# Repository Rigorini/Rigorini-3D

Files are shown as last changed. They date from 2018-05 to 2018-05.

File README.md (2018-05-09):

# Rigorini 3D
A big, cheap and accurate dual extruder FDM 3D Printer.

You can build it under 400,00 €!!

***

[Check the WIKI to understand the key features!](https://github.com/Rigorini/Rigorini-3D/wiki)

***

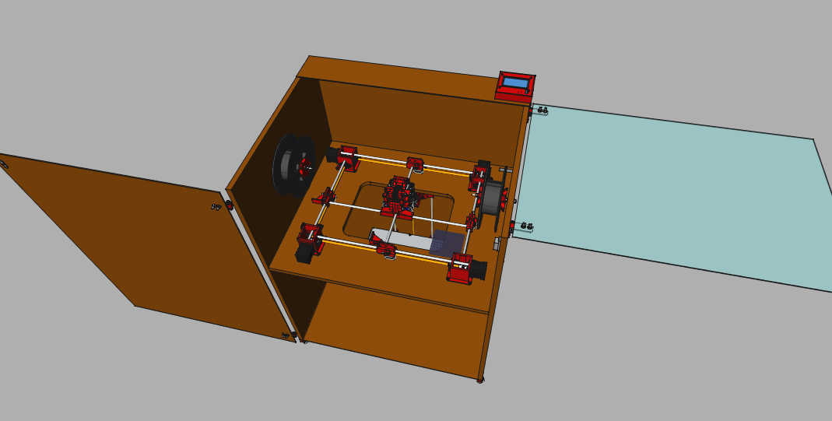
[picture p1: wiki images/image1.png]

Opened view

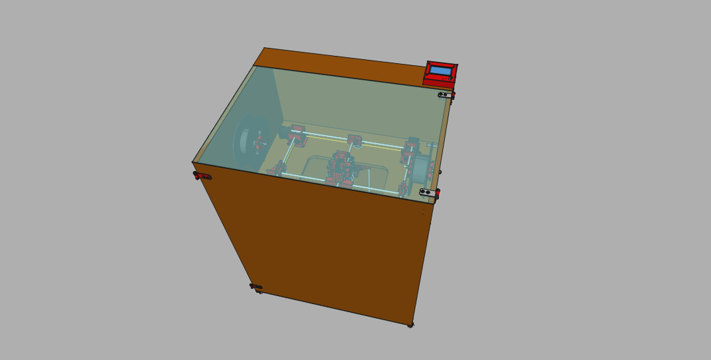
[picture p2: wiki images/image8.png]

Closed view

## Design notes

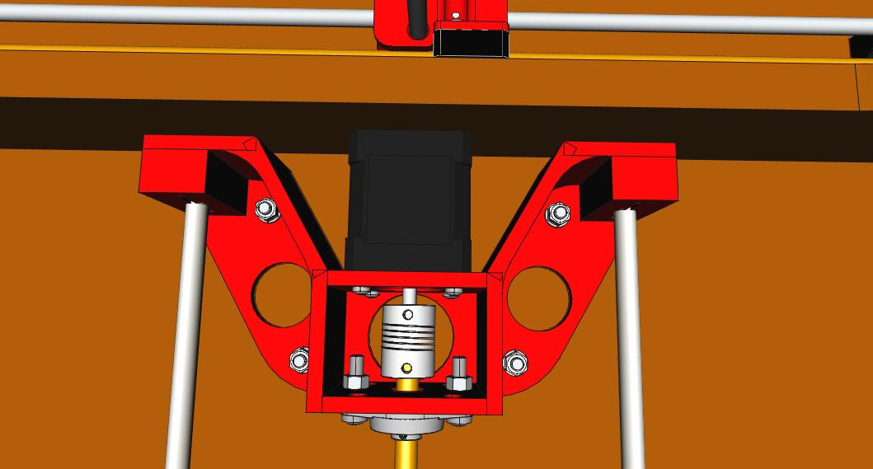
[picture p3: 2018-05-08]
wiki images/images12.png

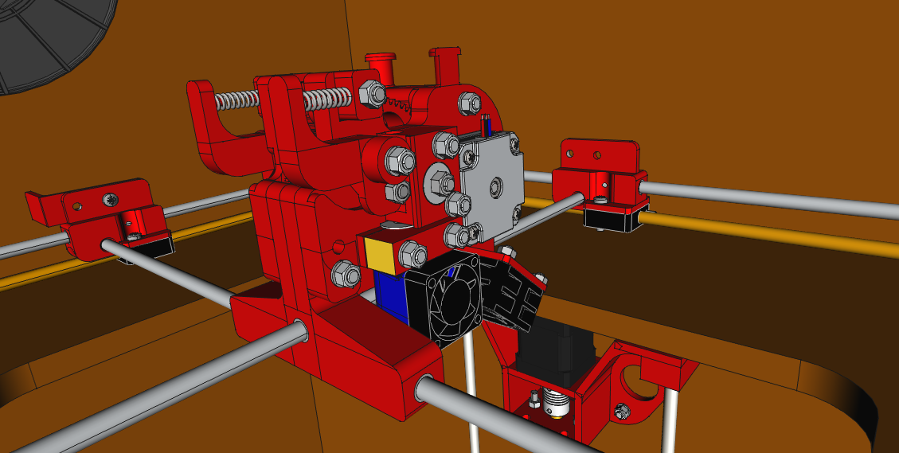
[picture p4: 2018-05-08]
wiki images/images9.png

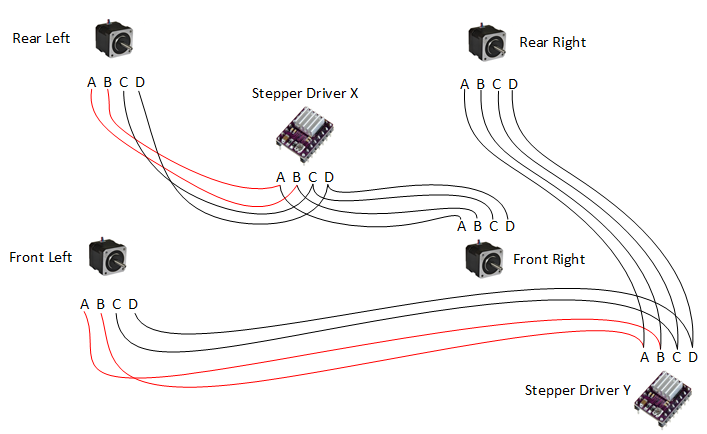
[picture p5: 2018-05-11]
wiki images/Steppers Schema.png

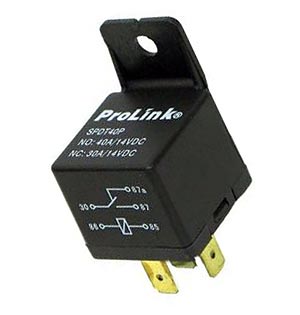
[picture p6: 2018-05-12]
wiki images/Relay.jpg

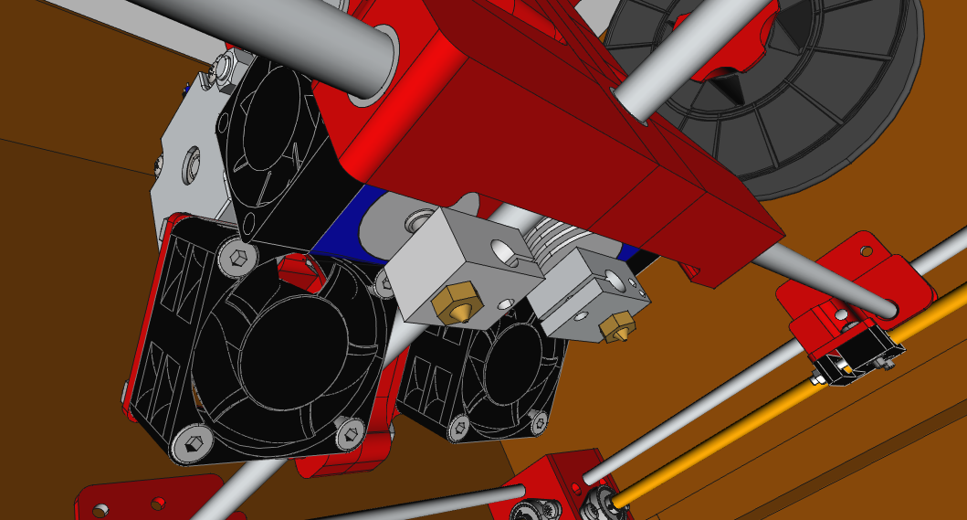
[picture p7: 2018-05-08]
wiki images/images11.png

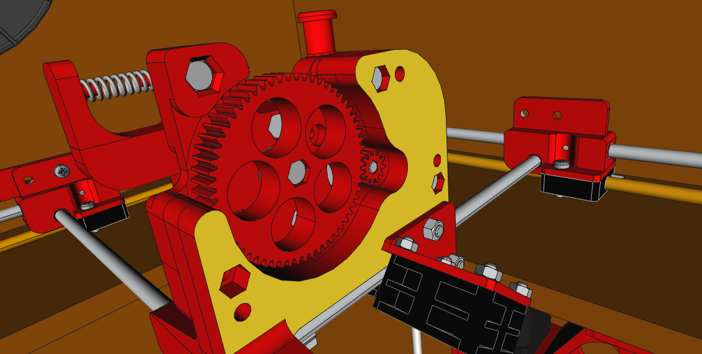
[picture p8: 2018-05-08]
wiki images/images10.png

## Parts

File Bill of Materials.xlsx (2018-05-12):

Description | Quantity | Where to buy | Estimate unit price | Total price
Alluminium sheet 215x315x2 | 1 | Local store | 3.00 € | 3.00 €
Arduino Mega 2560 | 1 | Aliexpress | 10.00 € | 10.00 €
Bearings 625zz | 10 | Aliexpress | 0.15 € | 1.50 €
Bearings KFL08 | 10 | Aliexpress | 1.50 € | 15.00 €
Bed level Spring | 3 | Aliexpress | 0.50 € | 1.50 €
Bolts 5x20 | 6 | Local store
Bolts 5x30 | 33 | Local store
Bolts 5x40 | 2 | Local store
Bushing Sleeve SF-1 0810 | 16 | Aliexpress | 0.28 € | 4.40 €
DRV8825 Stepper Driver | 5 | Aliexpress | 1.00 € | 5.00 €
Endstop Mechanical Switches | 3 | Aliexpress | 1.50 € | 4.50 €
Extruder E3D V6 with Fan (Direct) | 2 | Aliexpress | 6.00 € | 12.00 €
Fan 40x40x20 12V 3.8W | 2 | Aliexpress | 5.00 € | 10.00 €
Flat head Screw M3x30 | 3 | Local store
Flexible Shaft Coupler 8-5 | 5 | Aliexpress | 1.00 € | 5.00 €
Foot M10 | 4 | Local store
Gear Brass Feeder MK8 | 2 | Aliexpress | 1.00 € | 2.00 €
Hand Nuts for bed level M3 | 3 | Aliexpress | 0.50 € | 1.50 €
Hexagon Cilinder Screws M3x16 | 4 | Local store
Hexagon Head Cap Screws M4x25 | 4 | Local store
Leadscrew pitch 2mm 4 starts 366mm | 2 | Aliexpress | 8.00 € | 16.00 €
Leadscrew pitch 2mm 4 starts 687mm | 2 | Aliexpress | 8.00 € | 16.00 €
Leadscrew T8 350mm pitch 2 1 start + LeadScrew Nut | 1 | Aliexpress | 8.00 € | 8.00 €
Magnetic Lock with plate | 1 | Local store
Motors Nema 17HS08-1004S | 2 | https://www.omc-stepperonline.com | 10.40 € | 20.80 €
Notors Nema 17HS19-0854S | 5 | https://www.omc-stepperonline.com | 12.90 € | 64.50 €
Nuts M10 | 4 | Local store
Nuts M3 | 23 | Local store
Nuts M4 | 4 | Local store
Nuts M5 | 89 | Local store
Openbuilds Anti-Backlash Nut with screws | 4 | Aliexpress | 5.00 € | 20.00 €
Pan Head Screw M3x20 | 12 | Local store
Power Cord C13 | 1 | Local store | 3.00 € | 3.00 €
Power Inlet C14 With Switch | 1 | Aliexpress | 1.00 € | 1.00 €
Power Supply 12v 30A 360W | 1 | Aliexpress | 25.00 € | 25.00 €
Ramps 1.4 | 1 | Aliexpress | 5.00 € | 5.00 €
Ramps RRD Fan Extender | 1 | Aliexpress | 3.00 € | 3.00 €
Rectified 8mm rod 389mm (Right & Left) | 2 | Local store | 2.00 € | 4.00 €
Rectified 8mm rod 402mm (Axis Y) | 1 | Local store | 2.00 € | 2.00 €
Rectified 8mm rod 500mm (Axis Z) | 2 | Local store | 2.00 € | 4.00 €
Rectified 8mm rod 510mm (Back & Front) | 2 | Local store | 2.00 € | 4.00 €
Rectified 8mm rod 523mm (Axis X) | 1 | Local store | 2.00 € | 2.00 €
Relay 12V 40A | 1 | Local Car Parts Store | 5.00 € | 5.00 €
RepRap Heat bed 200x300 | 1 | Aliexpress | 35.00 € | 35.00 €
RepRap LCD 12864 | 1 | Aliexpress | 10.00 € | 10.00 €
Screw M3x8 | 28 | Local store
Screw M5x16 | 1 | Local store
Screw M5x16 | 2 | Local store
Screw M5x20 | 34 | Local store
Spring for feeder | 2 | Aliexpress | 0.50 € | 1.00 €
Tape Heat Resistant 10mm | 1 | Aliexpress | 2.00 € | 2.00 €
Threaded Rod M5 130mm | 2 | Local store
Top acrylic glass 500x752 | 1 | Local store | 7.00 € | 7.00 €
Washers M5 | 55 | Local store
Washers M5 Extra large | 4 | Local store
Wood Screws 2.2x9.5 | 6 | Local store
Wood Screws 4x12 | 49 | Local store
Wood Screws 4x30 | 18 | Local store
MDF Panels for case 16mm 610x930 | 4 | Leroy Merlin | 7.50 € | 30.00 €
MDF Panels for case 3mm 760x1060 | 2 | Leroy Merlin | 5.30 € | 10.60 €
MDF Panels for case 10mm 330x230 | 1 | Leroy Merlin | 3.00 € | 3.00 €
Estimated price for all nuts, screws, bolt, washers etc.. |  |  |  | 15.00 €
TOTAL |  |  |  | 392.30 €

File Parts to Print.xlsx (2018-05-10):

Part number | Number of copies | Material
Part 001 | 4 | PETG
Part 002 | 4 | PETG
Part 003 | 4 | PETG
Part 004 | 4 | PETG
Part 005 | 4 | PETG
Part 006 | 1 | PETG
Part 007 | 1 | PETG
Part 008 | 1 | PETG
Part 009 | 1 | PETG
Part 010 | 4 | PETG
Part 011 | 1 | PETG
Part 012 | 1 | PETG
Part 013 | 1 | PETG
Part 014 | 1 | PETG
Part 015 | 1 | PETG
Part 016 | 1 | PETG
Part 017 | 1 | PETG
Part 018 | 1 | PETG
Part 019 | 1 | PETG
Part 020 | 2 | PETG
Part 021 | 2 | PETG
Part 022 | 1 | PETG
Part 023 | 1 | PETG
Part 024 | 2 | ABS
Part 025 | 2 | ABS
Part 026 | 2 | PETG
Part 027 | 1 | PETG
Part 028 | 1 | PETG
Part 029 | 1 | PETG

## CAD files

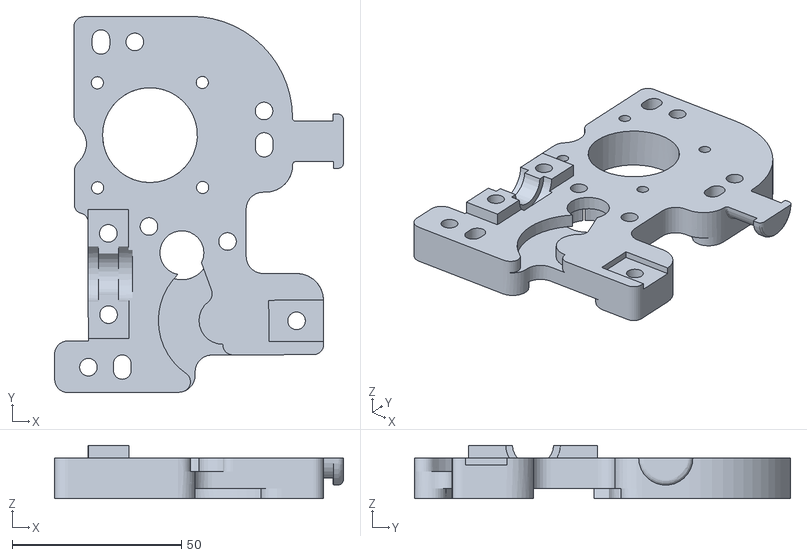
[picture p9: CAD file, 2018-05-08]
Model to be printed/Part 015 - Extruder Main Support Left.stl
85.3 x 111.1 x 15.8

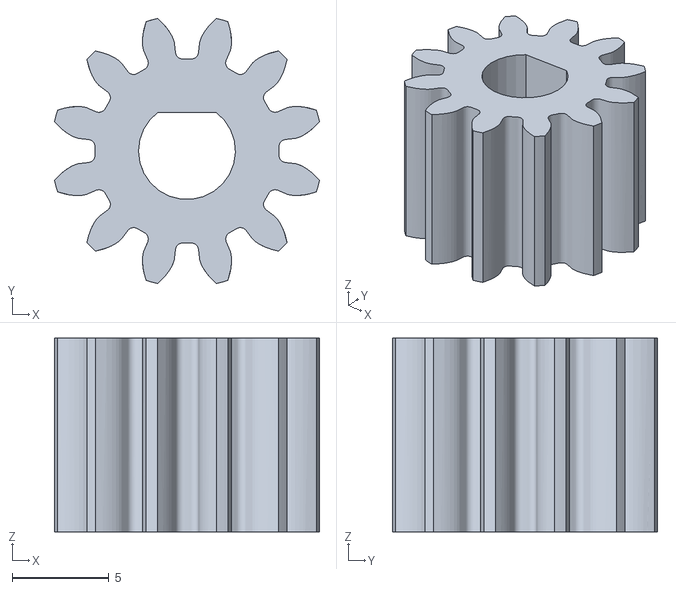
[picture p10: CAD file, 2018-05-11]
Model to be printed/Part 025 - Little Extruder Gear.stl
13.7 x 13.7 x 10.00

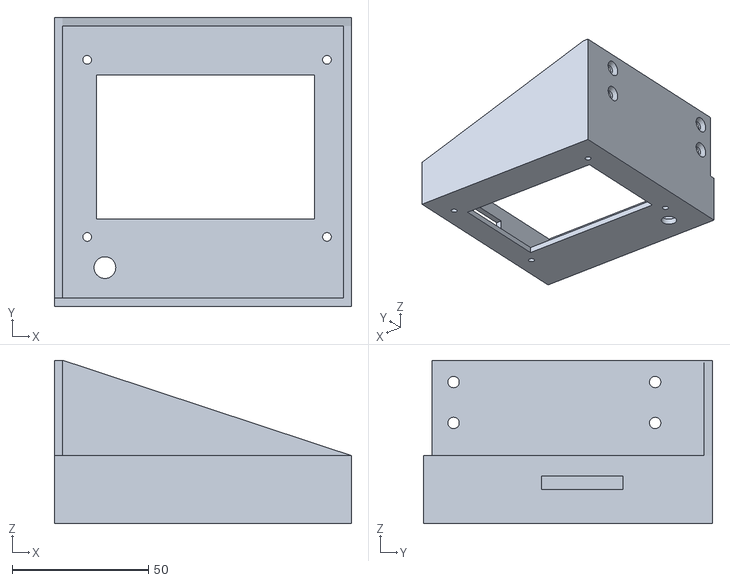
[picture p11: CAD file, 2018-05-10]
Model to be printed/Part 029 - LCD Case.stl
109.0 x 106.0 x 60.0

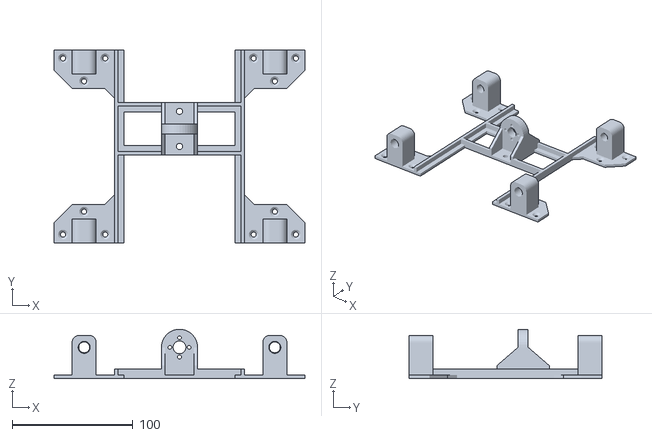
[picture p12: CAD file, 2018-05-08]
Model to be printed/Part 028 - Bed Skeleton.stl
208.0 x 160.0 x 41.0

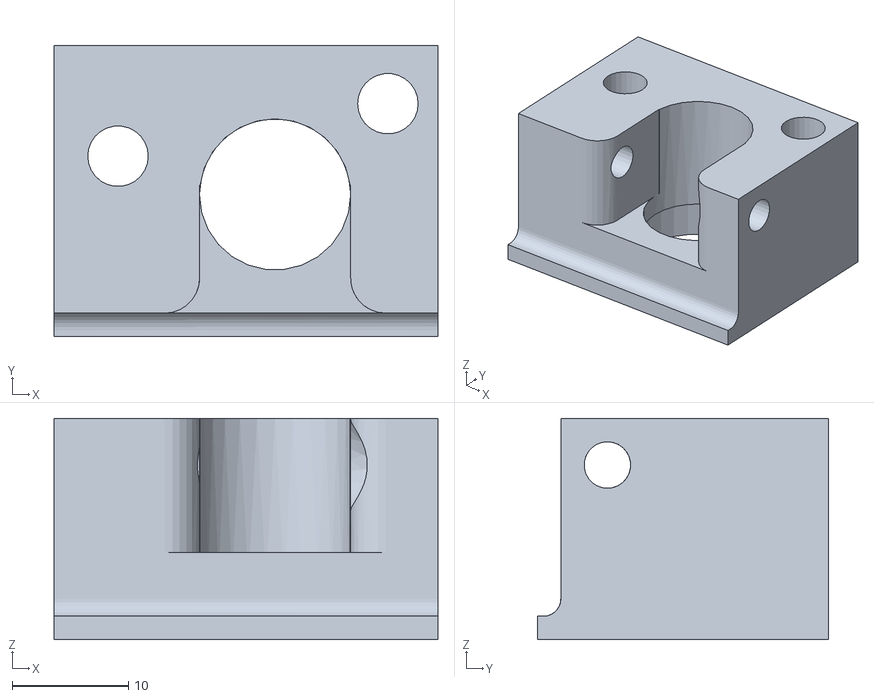
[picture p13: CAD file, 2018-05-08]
Model to be printed/Part 018 - Feeder Block Left.stl
33.0 x 25.0 x 19.0

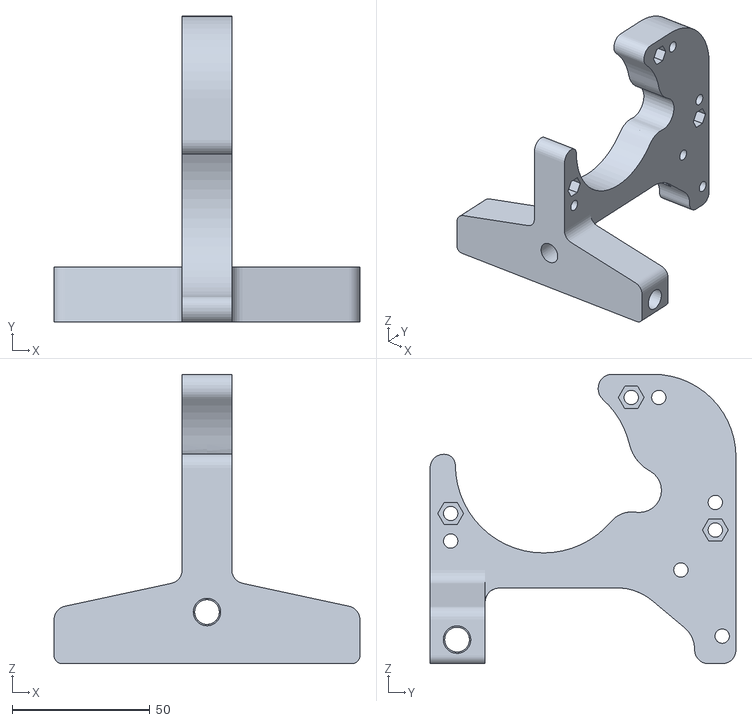
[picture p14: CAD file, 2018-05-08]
Model to be printed/Part 013 - Extruder Core.stl
111.0 x 111.0 x 105.0

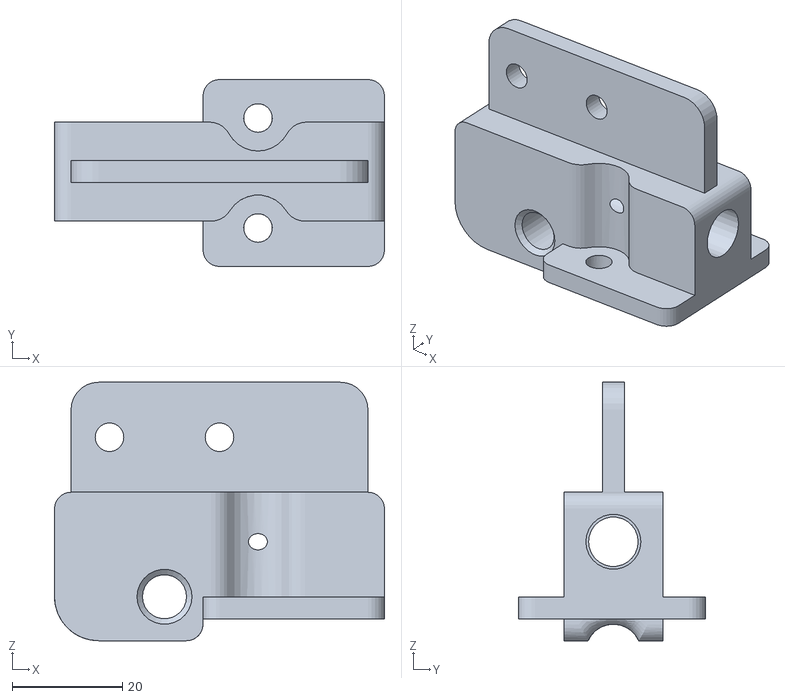
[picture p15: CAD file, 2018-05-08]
Model to be printed/Part 010 - Cursor XY.stl
60.0 x 34.0 x 47.0

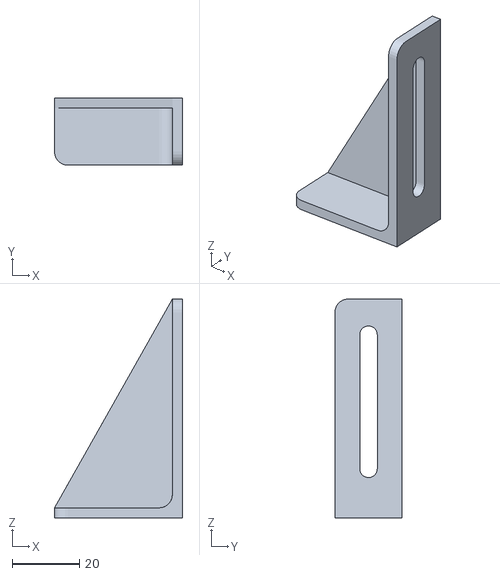
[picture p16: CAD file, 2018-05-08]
Model to be printed/Part 012 - Endstop Pusher Y.stl
38.0 x 20.0 x 65.0

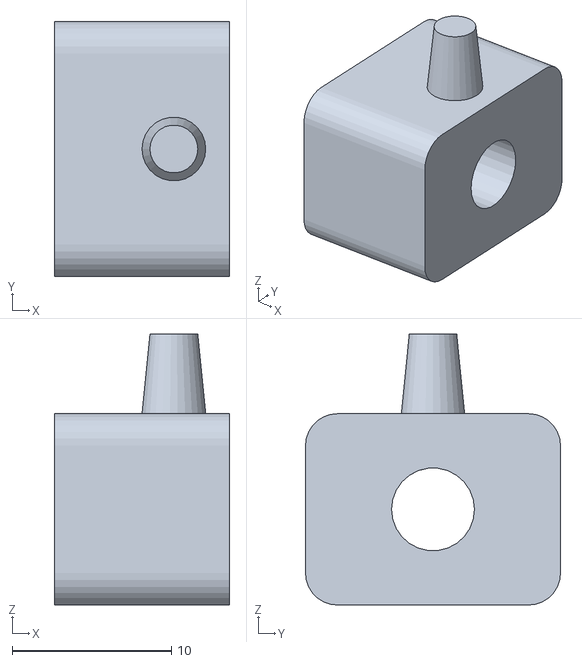
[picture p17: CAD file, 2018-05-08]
Model to be printed/Part 020 - Spring Base.stl
11.0 x 16.0 x 17.0

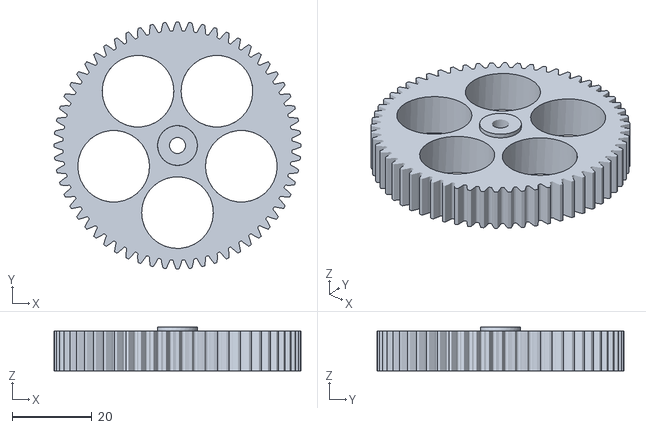
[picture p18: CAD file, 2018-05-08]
Model to be printed/Part 024 - Big Extruder Gear.stl
62.0 x 62.0 x 11.0

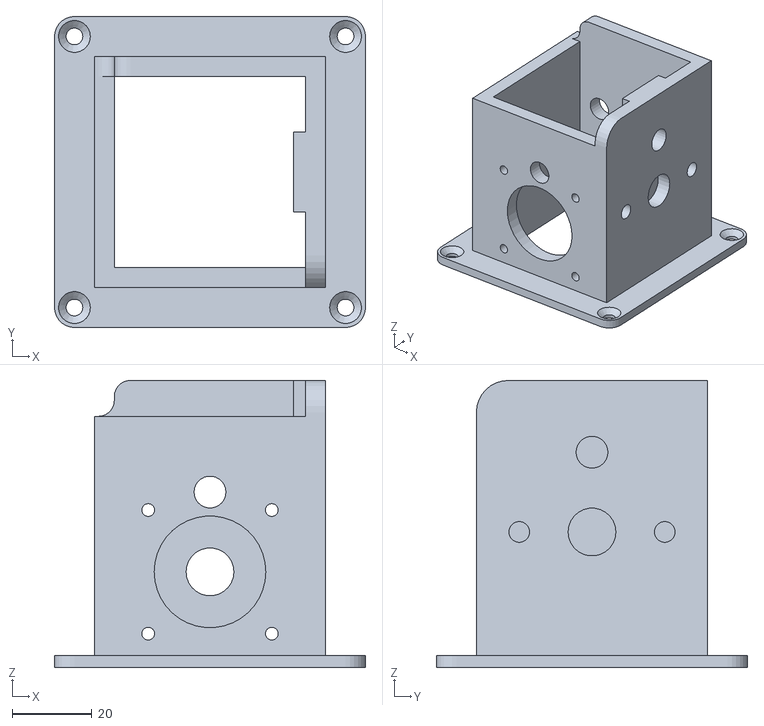
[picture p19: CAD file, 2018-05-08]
Model to be printed/Part 007 - Corner Support Front Left.stl
78.0 x 78.0 x 72.0

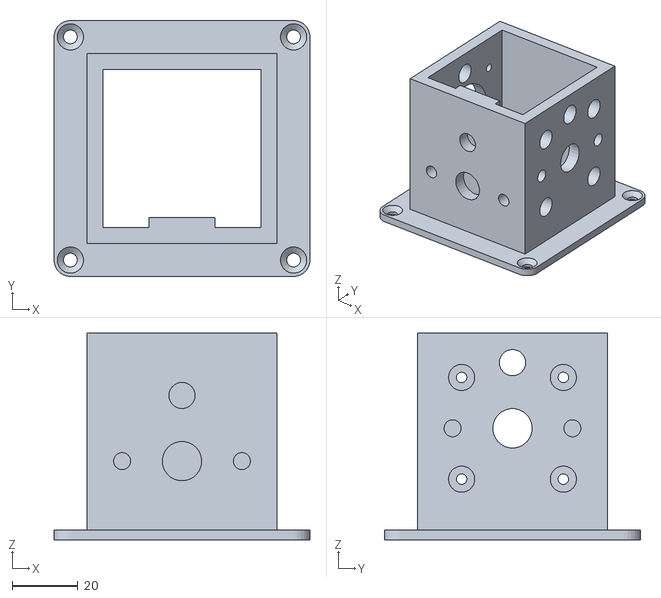
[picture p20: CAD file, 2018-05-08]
Model to be printed/Part 006 - Corner Support Rear Left.stl
78.0 x 78.0 x 63.0

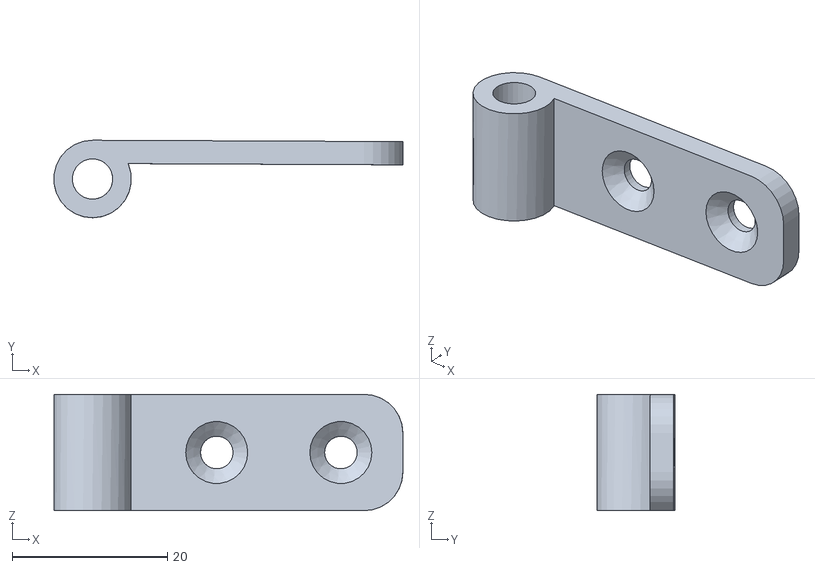
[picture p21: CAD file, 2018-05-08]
Model to be printed/Part 004 - Hinge Fixed.stl
45.0 x 10.0 x 15.0

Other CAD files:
Model to be printed/Part 014 - Extruder Main Support Right.stl
Case Drawings.dwg
Model to be printed/Part 011 - Endstop Pusher X.stl
Model to be printed/Part 009 - Corner Support Front Right.stl
Model to be printed/Part 008 - Corner Support Rear Right.stl
Model to be printed/Part 001 - Foot Support Bottom.stl
Model to be printed/Part 002 - Foot Support Top.stl
Model to be printed/Part 003 - Spool Cone.stl
Model to be printed/Part 005 - Hinge Mobile.stl
Model to be printed/Part 016 - Filament Pusher Right.stl
Model to be printed/Part 017 - Filament Pusher Left.stl
Model to be printed/Part 019 - Feeder Block Right.stl
Model to be printed/Part 021 - Lock collar Extruder.stl
Model to be printed/Part 022 - Fan Holder Right.stl
Model to be printed/Part 023 - Fan Holder Left.stl
Model to be printed/Part 026 - Z Axis Support.stl
Model to be printed/Part 027 - Z Endstop Support.stl

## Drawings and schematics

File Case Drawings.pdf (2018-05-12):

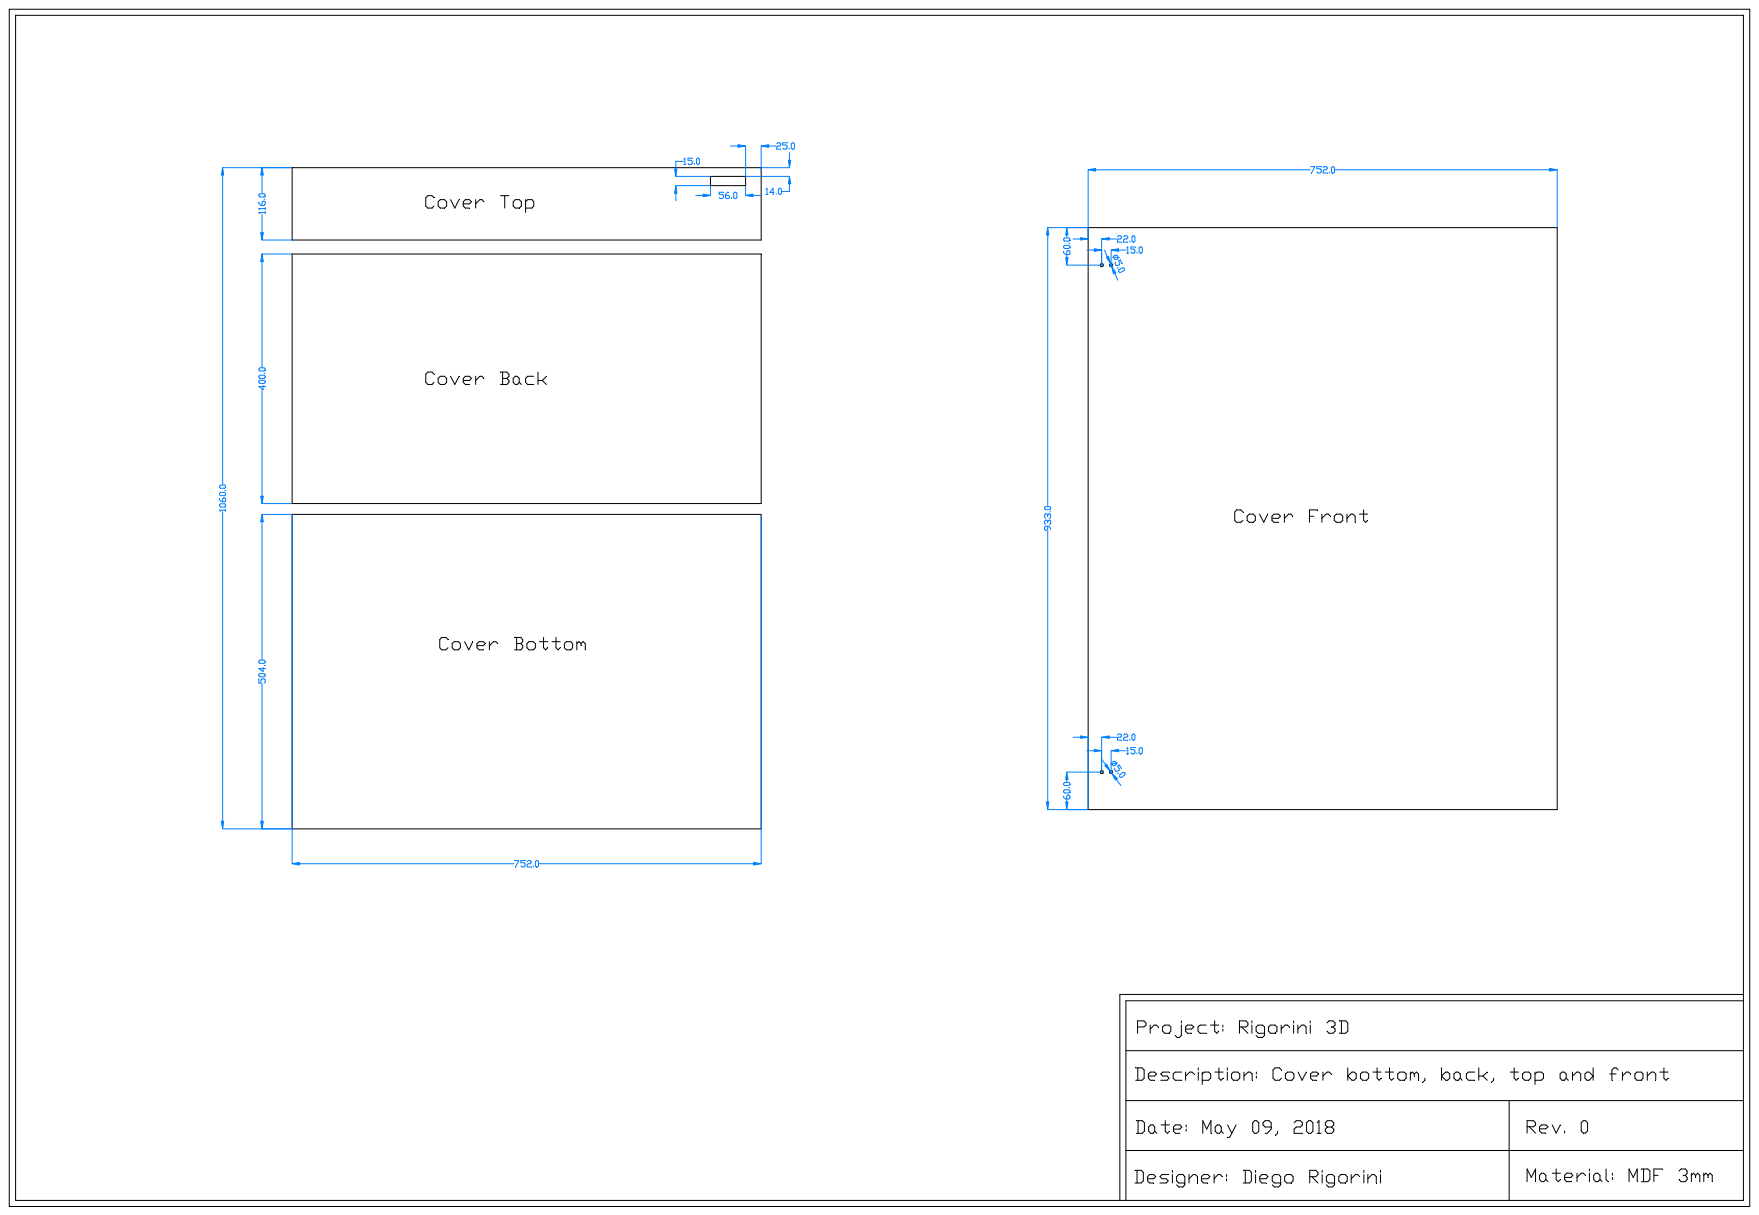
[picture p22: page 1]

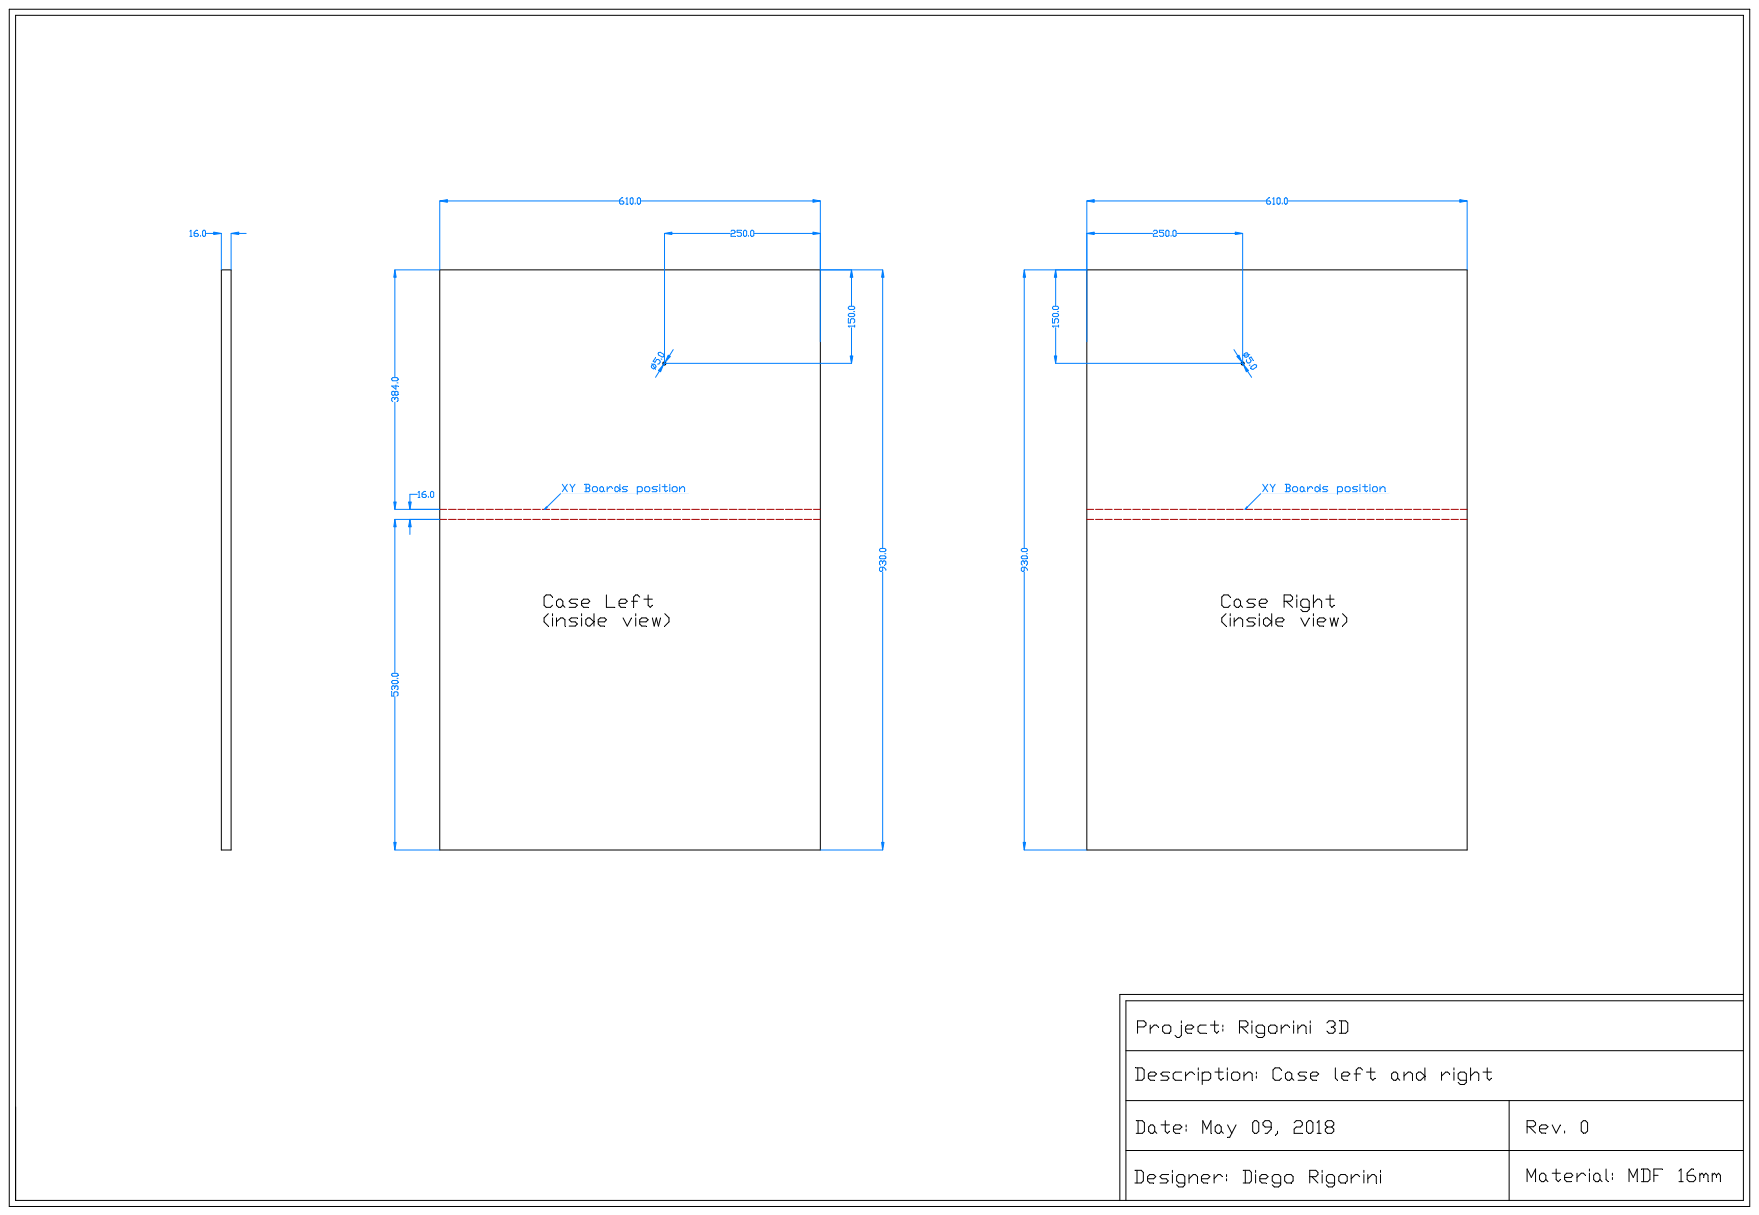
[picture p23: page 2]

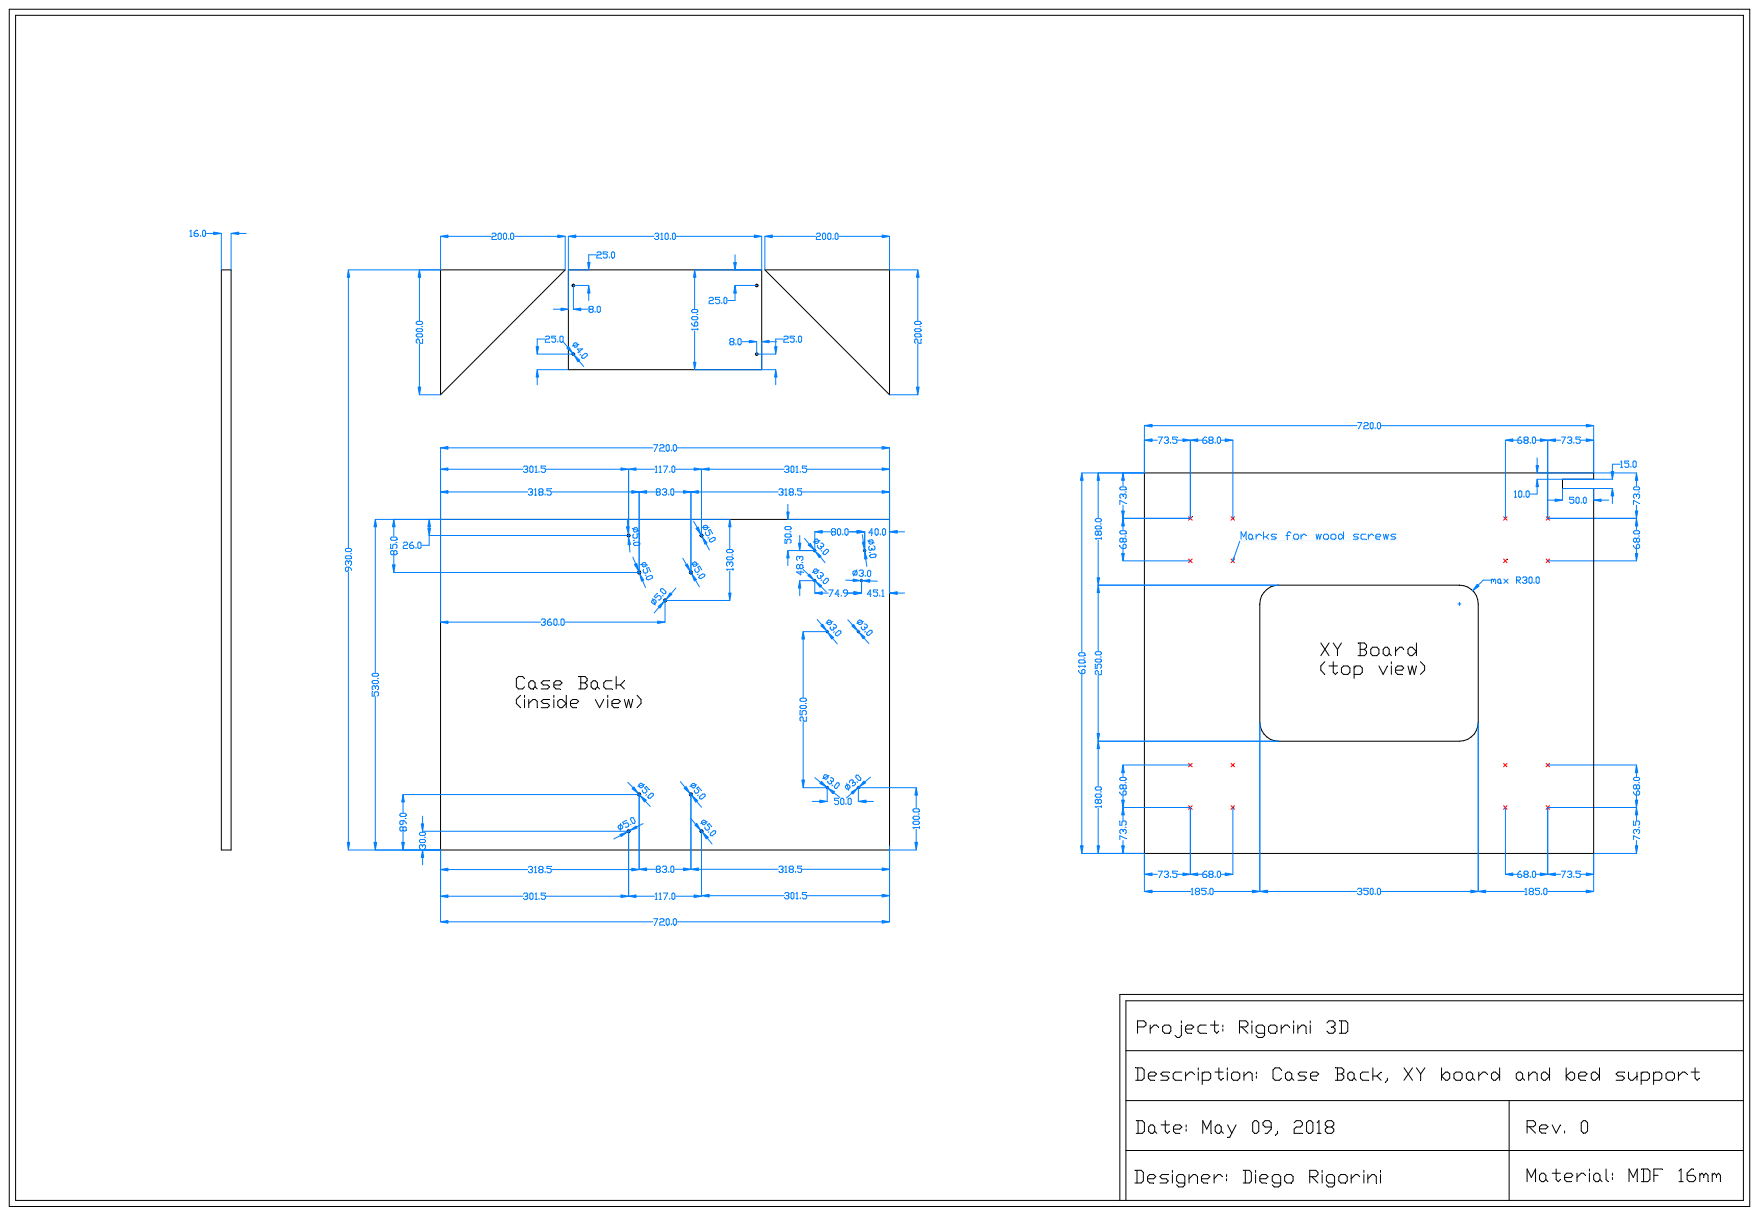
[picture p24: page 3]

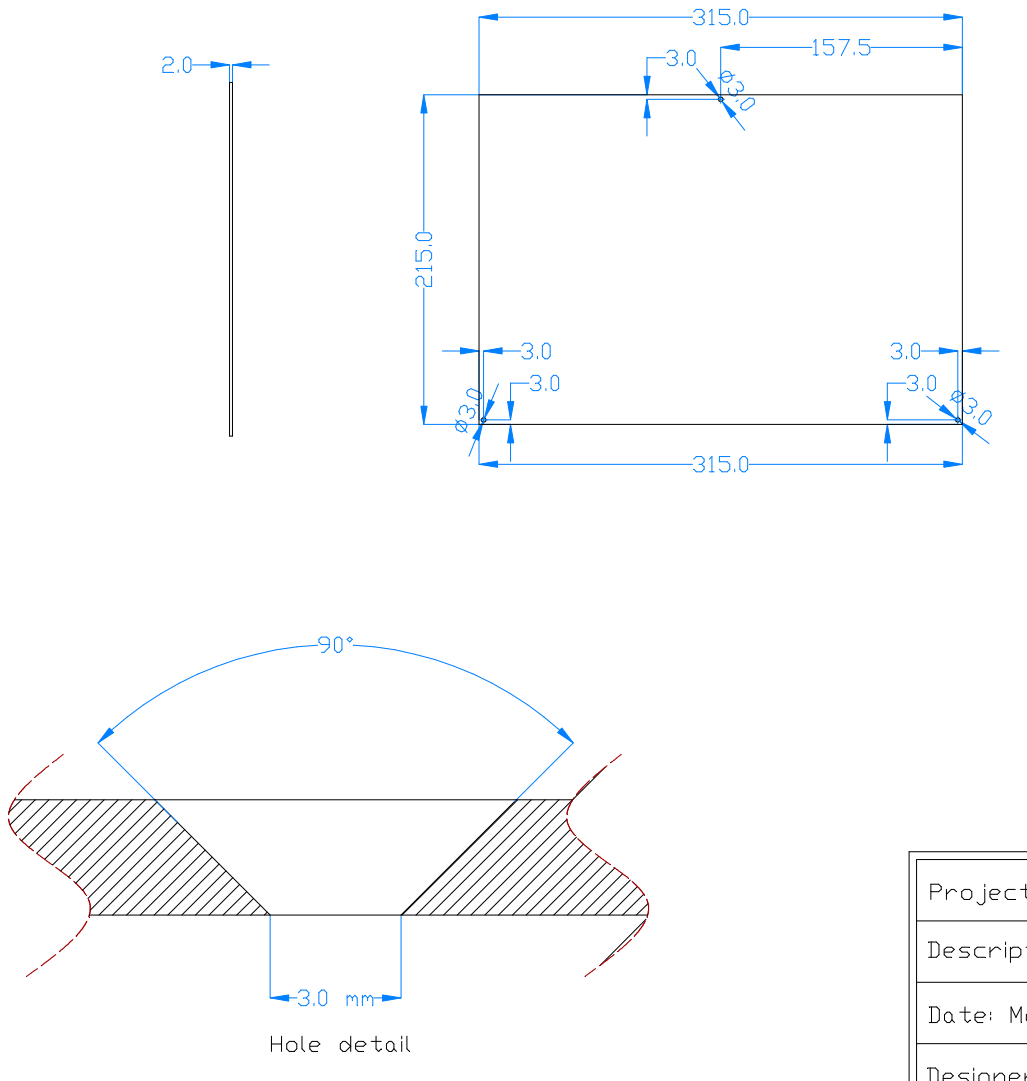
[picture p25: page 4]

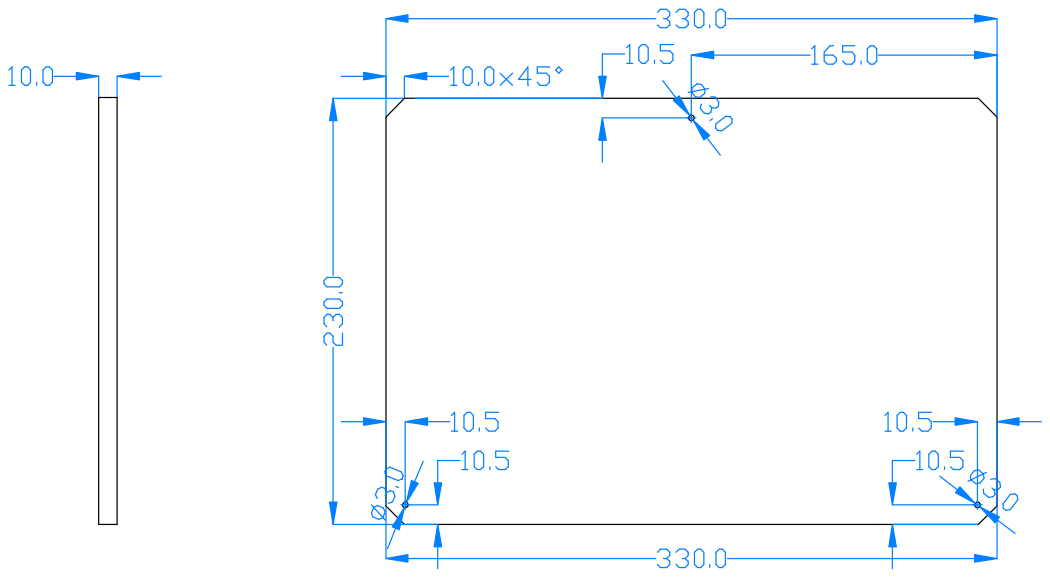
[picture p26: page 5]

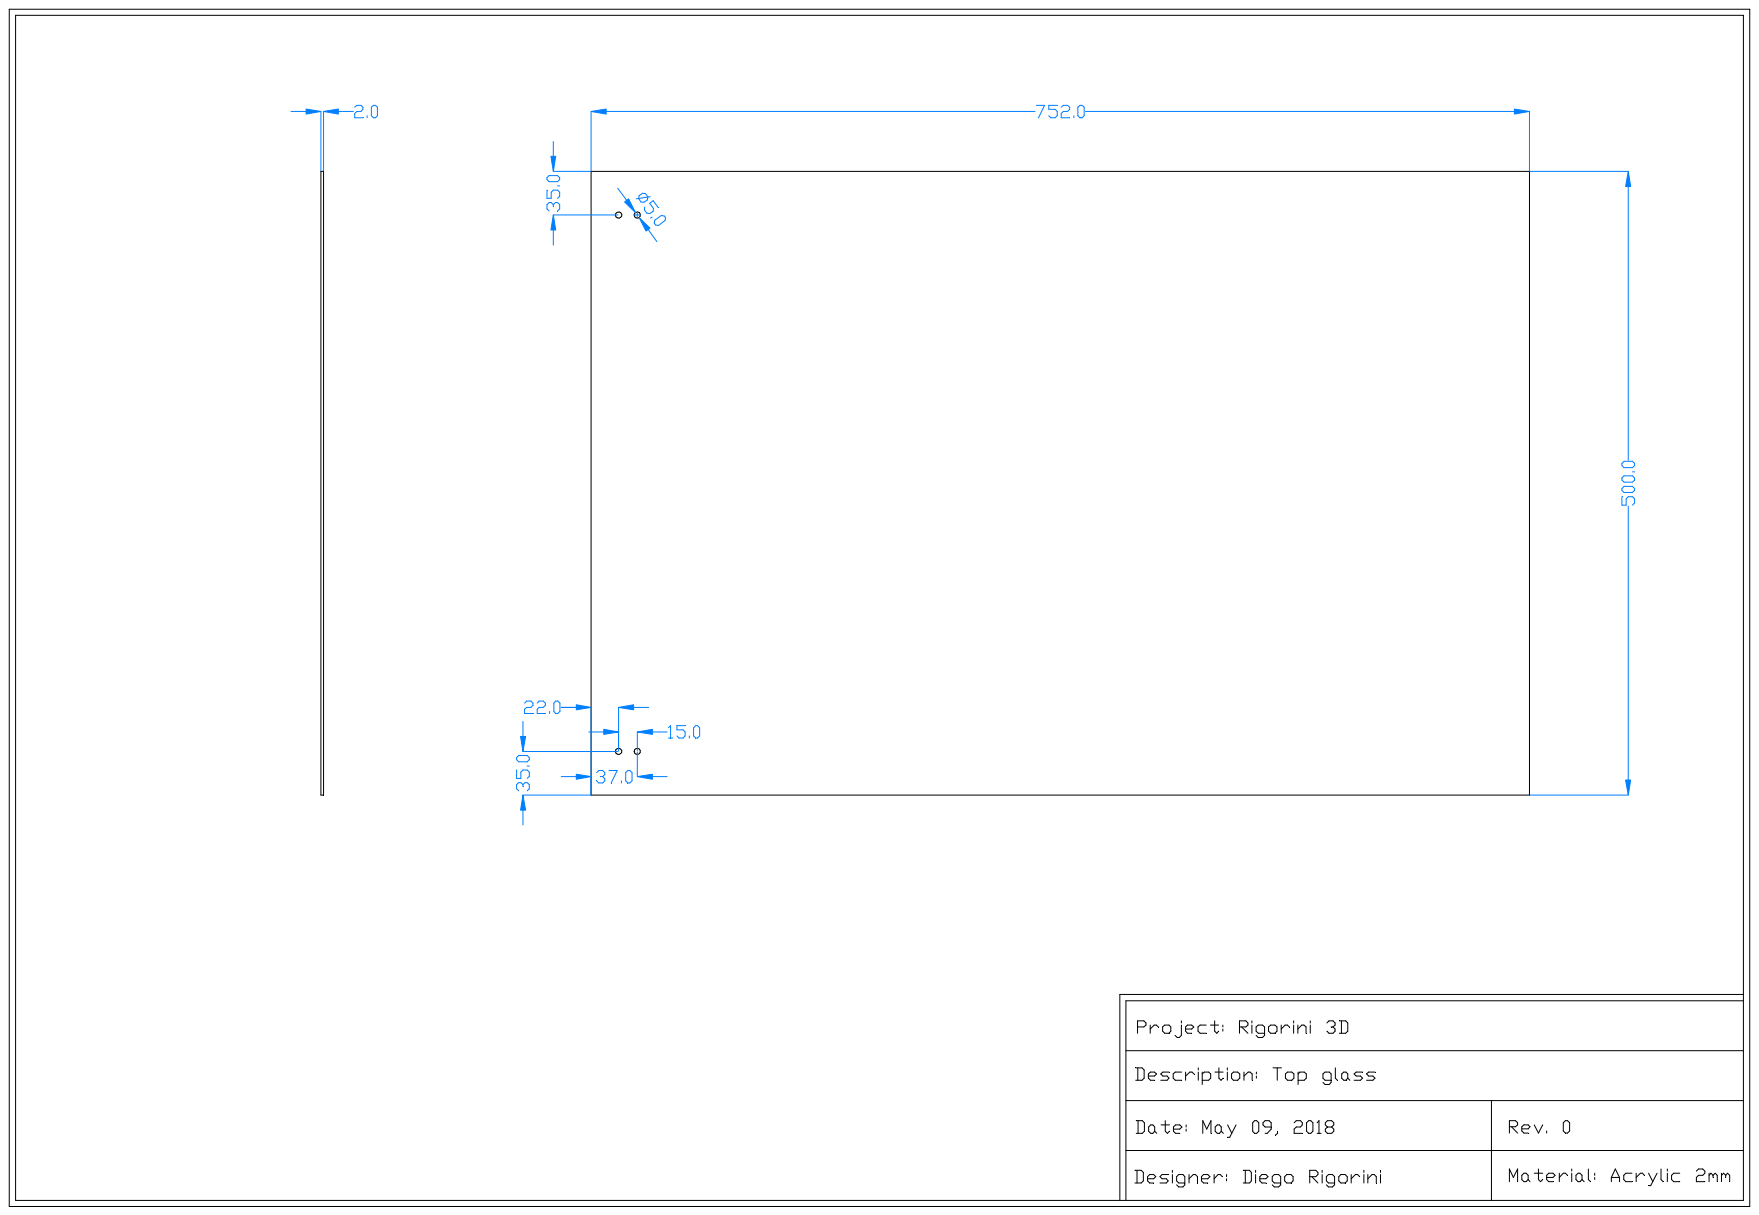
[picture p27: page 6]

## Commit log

2018-05-07 Trapezoidal screws difference
2018-05-07 Hole for horizontal extruder adjusting
2018-05-07 Hole for vertical extruder adjusting
2018-05-07 KFL08 Bearings for trapezioidal screws
2018-05-07 Inlet power
2018-05-07 Closed printer
2018-05-08 Part to be printed
    [Part 001 - Foot Support Bottom.stl, Part 002 - Foot Support Top.stl, Part 003 - Spool Cone.stl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]
2018-05-08 List of parts to print with quantity and material
    [Parts to Print.xlsx]
2018-05-08 Part to print
    [Part 028 - Bed Skeleton.stl]
2018-05-09 Drawing of the case in PDF Format
2018-05-09 Drawings of the case in DWG format
    [Case Drawings.dwg]
2018-05-09 Drowing of the case in PDF format
2018-05-09 List of materials with price and where to buy
    [Bill of Materials.xlsx]
2018-05-09 Drawings of the case in PDF format
2018-05-10 Part to be printer
    [Part 029 - LCD Case.stl]
2018-05-10 List of parts to print
    [Parts to Print.xlsx]
